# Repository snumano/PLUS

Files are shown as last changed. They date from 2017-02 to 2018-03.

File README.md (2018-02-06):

# Otto DIY+
"Otto DIY with steroids" 

This Repository have all open source files for Otto DIY+ an interactive robot that anyone can make!,
Otto DIY + can make everything that Otto DIY does + Bluetooth + APP + switch + sensors + strength +... anything you might expand feel FREE to add and contribute. for LED Matrix we have a separate repository here https://github.com/OttoDIY/Matrix_hands
Is completely open source, Arduino compatible, 3D printable, once you have all components and tools you will be able to build your own Otto
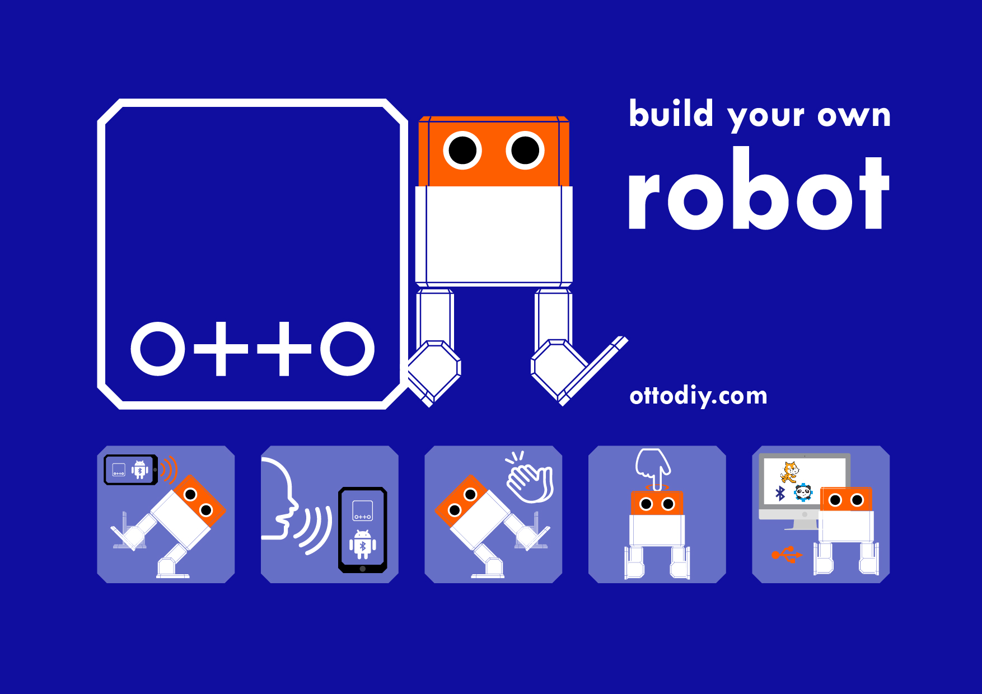
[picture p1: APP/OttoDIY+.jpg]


This is a more advanced version requires some expertise and patience, if you want to start slow as a beginner  please go to [Otto DIY repository](https://github.com/OttoDIY/DIY)

Start by [downloading all files here](https://github.com/OttoDIY/PLUS/archive/master.zip)

## For the hardware
Gather all the off the shelf parts in the BOM file that you'll need for this assembly, then 3d print the  .stl files and then follow the instruction manual to build your own robot.

## For the quick start programming and learners
1. download mBlock.cc V3; is an opensource software released by MakeBlock for easy programming Robot by Drop and Drag blocks. Based on Scratch 2.0 (MIT), beside sharing the great Feature of Scratch, mBlock also integrated an Arduino Code generator for upload program into Arduino based Hardware.
2. install Otto Extension in mBlock software use Arduino mode
3. drag and drop functions, dance, sounds and conditionals from robot Otto blocks
4. connect and check COM port
5. upload your own code! 

## For the advanced programming
1. Download & Install Arduino IDE: https://www.arduino.cc/en/Main/Software also this driver if you have a clone board: http://www.wch.cn/download/CH341SER_EXE.html for PC, or http://www.wch.cn/download/CH341SER_MAC_ZIP.html for MAC
2. Copy all libraries to C:\Users\user\Documents\Arduino\libraries (or wherever your library folder is installed):
3. Open  any .ino code, make sure in tools you have "Board: Arduino Nano" "Processor ATmega328" and your Otto is connected to the corresponding port
4. Upload code to your Otto
5. Check or setup your Bluetooth module baud rate
6. Upload the Bluetooth APP code to Otto DIY+
7. Play with the APP
8. Share in our Otto builder Facebook group https://www.facebook.com/ottodiy/groups/

### Otto DIY+ is  design using Autodesk Fusion 360
So is completely parametric and precise to adjust tolerances
[You can modify it for customization](https://gallery.autodesk.com/fusion360/projects/otto-diyplus) or further improvements

### Hall of fame Otto builders list
Our broad community is awesome! we have been developing and improving OttoDIY project together ;)

| contribution  | date | builder name | country |
| --- | --- | --- | --- |
| oscillator algorithm library| Jan 2015 | Obijuan | Spain  |
| inventor of Zowi 3D printable | Dec 2015  | Javier Isabel |Spain |
| Bobwi (combination of Bob and Zowi  | Jan 2016  |G4alileo |Spain  |
| BT, battery, nose LED RGB, touch and tilt | April 2016 |Davor Levstek  |Croatia |
| Robonino with voice control |May 2016|Santiago|Spain |
| Calibration tool  | June 2016 |Rafael López  |Spain |
| FreeCAD model|August 2016|Juan Carlos López Sánchez |Spain |
| ESPOtto voice | Sept 2016 |Gustavo Reynaga |Mexico|
| Otto arms |Sept 2016|Jason Leung| Hong Kong |
| Google Play android APP  | Oct 2016 |Juan Felix Mateos |Spain |
| Switch alternative |Dec 2016|Robert Holt |United States |
| Custom PCB, OttoDIY+ repository | Jan 2017 |Jason Snow |England |
| Single ladies dance| Jan 2017  |brico3D |Spain |
| Nose and DIY APP |Feb 2017|Andrés Fernández Muñoz|Spain |
| feedback  | March 2017 |Frank Lopez |United States |
| feedback | March 2017  |Octavio P Nogueira |Brazil  |
| feedback  | March 2017  |tritri62|??? |
| Custom PCB | 	March 2017 |Marco|Italy |
| Laser cut Otto |March 2017|Florian Festi|Germany |
| XXL Head |March 2017|Markus Otte |Germany |
| XGoBroRobo IR control |March 2017|Jonathan Hess |Germany |
| Easy BT Easy HC-06 | May 2017  |Pablo E. García Palacios  |Spain |
| Custom PCB, battery booster, noise detection | April 2017|Pedro 51|France |
| graphical coding  | June 2017  |Liao Ping Lun  |China |
| Otto bender mod| June 2017  |bricogeek |Spain |
| remote control | July 2017  |Jayesh Chauhan |India  |
| Customizable Otto 3D print |July 2017|Brandon Bowles |United States |
| quadruped Otto | August 2017  |quadruped |China |
| control from laptop | August 2017  |SungHyun Ryu |South Korea |
| touch code | September 2017  |Alberto |Spain |
| Otto wheels | September 2017 |Jason Snow |England |
| Tito +| September 2017 |Jason Snow |England |
| 6 modes code | October 2017  |Davor Levstek  |Croatia |
| Otto accessories| October 2017  |Lucid Wolf|Australia |
| Otto accessories Halloween  | October 2017  |Trish Davies  |Australia |
| mbloc scratch graphical coding| November 2017  |Hien Phan |Vietnam |
| Otto Santa Claus| December 2017  |Dreamfactory  |Argentina |
| Otto Nutcraker| December 2017  |Dreamfactory  |Argentina |
| SelfProgramming| December 2017  |YoJuLab  |South Korea |
| open APP inventor | January 2018 |Jason Snow |England |
| LED eyes | January 2018 |Mr. Chan|China |
| Otto learning| January 2018  |Hien Phan |Vietnam |
| new APP BETA | February 2018 |Jason Snow |England |

Special thanks to all these #Ottobuilder that made and are making this project evolve and accessible to everyoone in the world. If we skip one please tell us!

### Pending  to develop idea list
Feel free to grab and mix ideas from this table for your Otto and if you are nice person please share with all the community

| Function-Feature  | sensor(input) | movement (output) | 
| --- | --- | --- |
| drumer  |microphone|hands+stick|
| Car-balancing  |accelerometer|4x4 wheels|
| Sumo |IR|wheels+bumper|
| omniwheel |magnet switch|wheels+rollers|
| Train |IR|Steam generator|
| Humanoid |variable resistor modes|+servos control|
| Spider 6-8 legs |gestures|+vibrators|
| hover or drone |accelerometer|+DC motor control|
| look around xiaofang |timer|new head|
| writer |encoders|DC+ pen holder|
| following line |IR+encoders|step motors|
| Bubbles |light|DC fan|
| crane |Buttons|+servos control|
| Gripper |Tilt Sensor|+servo|
| reaction to music  |keepon|vibrators|
| Follow music | MP3 SD card|disco lights|
| Voice commands |telegram|multiple boards|
| clap rhythm |microphone|vibrators|

## License CC-BY-SA
<br /><span xmlns:dct="http://purl.org/dc/terms/" property="dct:title">Otto DIY</span> by <a xmlns:cc="http://creativecommons.org/ns#"  property="cc:attributionName"> [www.ottodiy.com](http://www.ottodiy.com) </a> is licensed under a <a rel="license" href="http://creativecommons.org/licenses/by-sa/4.0/">Creative Commons Attribution-ShareAlike 4.0 International License</a>.

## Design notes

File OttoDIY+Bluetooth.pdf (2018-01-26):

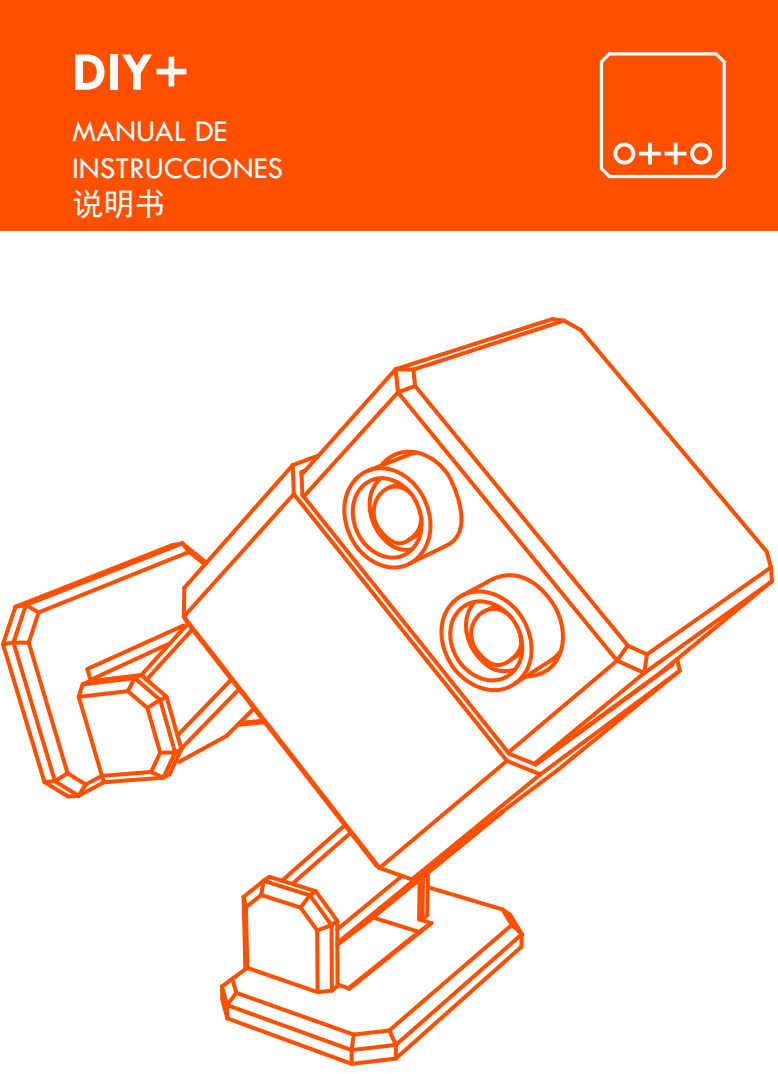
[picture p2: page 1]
DIY+; MANUAL DE INSTRUCCIONES 说明书

Estos pasos son para configurar los módulos de Bluetooth HC-05 y HC-06 Las conexiones son las siguientes:
HC-05 GND --- Arduino GND Pin
HC-05 VCC (5V) --- Arduino 5V
HC-05 TX --- Arduino Pin 10 (soft RX)
HC-05 RX --- Arduino Pin11 (soft TX)
HC-05 Key (PIN 34) --- Arduino Pin 9

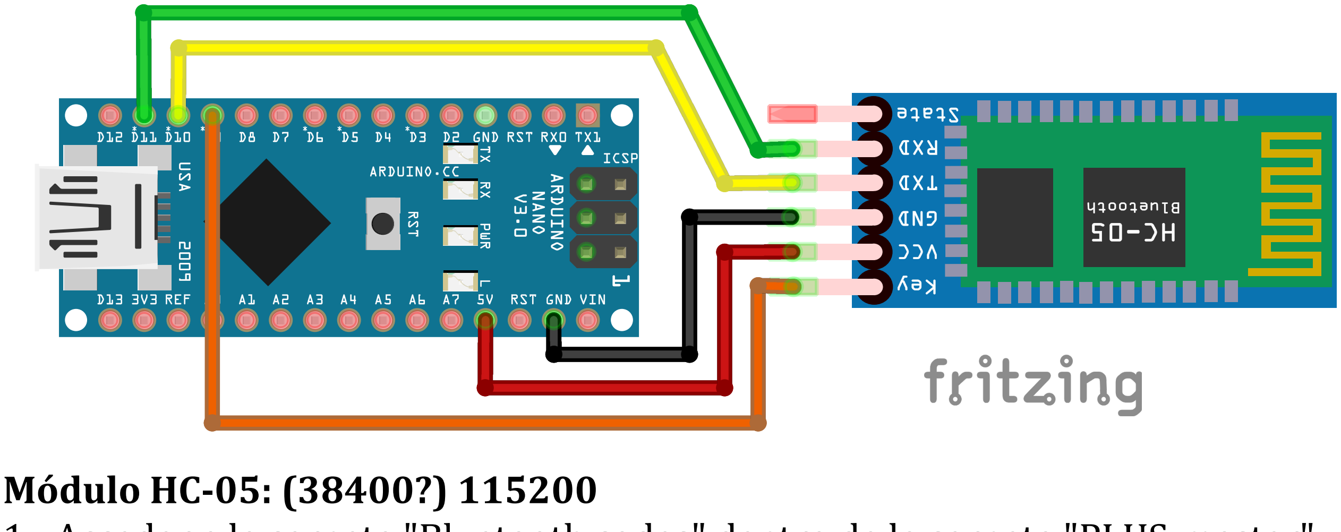
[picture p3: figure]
Módulo HC-05: (38400?) 115200

1.- Acceder a la carpeta "Bluetooth codes" dentro de la carpeta "PLUS-master" y cargar el código HC05_BT_Config.ino (https://github.com/OttoDIY/PLUS/blob/master/Bluetooth%20codes/HC05_BT_config/HC05_BT_config.ino) al Arduino Nano.
2.- Desconectar el Arduino Nano del USB y realizar la conexión del módulo de Bluetooth como se indica en la imagen de arriba, sin conectar aún el voltaje de alimentación VCC.
3.- Conectar de nuevo el Arduino Nano al USB y entonces conectar el cable del Bluetooth a VCC tal que entre en el modo de comando AT. El led del Bluetooth debería comenzar a destellar lentamente, al rededor de una vez cada 2 segundos. (si esto no llegara a suceder, intente mantener pulsado el botón de reset del módulo Bluetooth mientras lo alimenta a VCC)
4.- Abra el monitor serie de la IDE de Arduino, seleccione la tasa de transmisión a 9600 baudios, y en final de línea ambos NL & CR.
5.-Introduzca AT y presione Enter; (si todo es correcto, el Bluetooth debería responder con un OK y entonces proceder a introducir los siguientes comandos): AT+NAME=Zowi (Establecemos el nombre)
AT+PSWD=1234 (Establecemos el código de paridad) AT+UART=115200,1,0 (Establecemos la tasa de transmisión)
AT+POLAR=1,0 " ( Habilitamos el pin STATE para ser utilizado como reset para programar Arduino a través del módulo Bluetooth)
Por último, cerrar el monitor serie y realizar las conexiones electrónicas de Otto.

Módulo HC-06: (9600?) 115200
Para el módulo HC-06 las cosas son un poco más simples debido a que siempre se encuentra en modo de comando AT cuando no se encuentra conectado a nada. La desventaja es que el módulo HC-06 no puede ser usado para cargar códigos al Arduino debido a que no posee reset.
Para configurar el módulo:
1.- Cargar el código HC06_BT_config.ino (https://github.com/OttoDIY/PLUS/blob/master/Bluetooth%20codes/HC06_BT_config/HC06_BT_config.ino) al arduino Nano
2.- Desconectar el Arduino Nano del USB
3.- Conectar el módulo Bluetooth al Arduino Nano como se indica en la imagen de
abajo:
HC-06 GND --- Arduino GND Pin
HC-06 VCC (5V) --- Arduino 5V
HC-06 TX --- Arduino Pin RX
HC-06 RX --- Arduino Pin TX

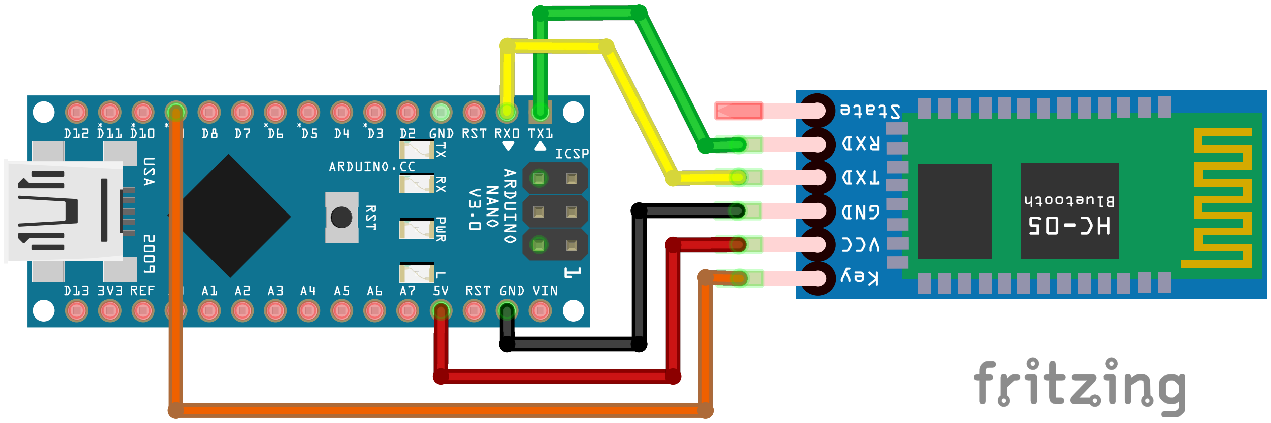
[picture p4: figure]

2.- Desconectar el Arduino Nano de la usb y realizar la conexión del módulo de Bluetooth como se indica en la imagen de arriba, sin conectar aún el voltaje de alimentación VCC.
3.- Encender el Arduino Nano y después de al rededor de 10 segundos todo debería estar terminado y tu módulo Bluetooth debería estar configurado (LED 13 debería comenzar a destellar).
Por último, realizar las conexiones electrónicas de Otto.

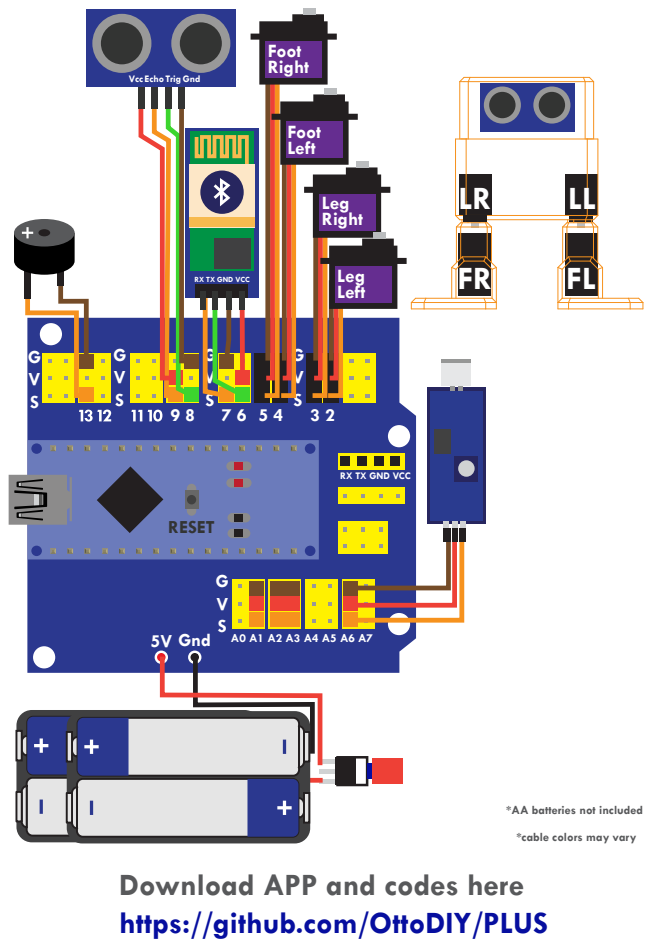
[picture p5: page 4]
RESET; 5V Gnd; Foot Right; FL RX TX GND VCC; Leg; Left; Leg Right; Foot Left; Vcc; TrigEcho; Gnd

RX TX GND VCC

*AA batteries not included
*cable colors may vary

Download APP and codes here
https://github.com/OttoDIY/PLUS

Código Principal
Después de configurar el módulo Bluetooth, desconecte de nuevo el módulo Bluetooth y cargue el siguiente código al Arduino Nano:
OTTO_BT.ino (https://github.com/OttoDIY/PLUS/blob/master/Bluetooth%20codes/OTTO_BT/OTTO_BT.ino)
Después de cargar exitosamente el código, conecte el módulo Bluetooth de nuevo y estará listo para el emparejamiento.

APP para Android:
Tú puedes crear tu propia APP!
Descarga la última APK aquí (https://github.com/OttoDIY/PLUS/tree/master/APP)
Usando la aplicación AppInventor desarrollada por el MIT, usa nuestra plantilla para modificar y crear tu propia aplicación móvil.
O debido a que Otto también es compatible con Zowi, tú puedes usar la APP desarrollada por BQ
Descarga Aquí la (https://play.google.com/store/apps/details?id=com.bq.zowi&hl=es) App Oficial de Zowi desarrollada por BQ
Descargue el código Otto_BT_ZowiAPP.ino (https://github.com/OttoDIY/PLUS/blob/master/Bluetooth%20codes/Otto_BT_ZowiAPP/Otto_BT_ZowiAPP.ino)
Instala y abre la APP Zowi para Android, empareja los dispositivos e ignora los mensajes de advertencia que dicen que el código fué modificado o similar. Nota: Recuerda copiar todas las librerías en la carpeta de Arduino

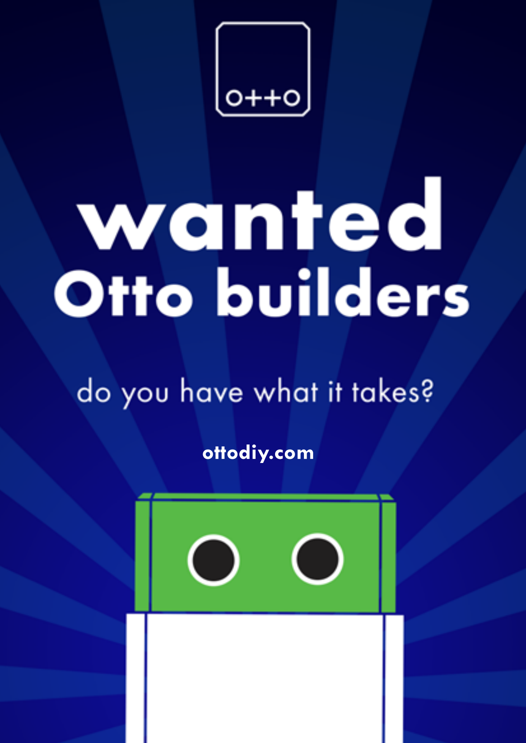
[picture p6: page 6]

ottodiy.com

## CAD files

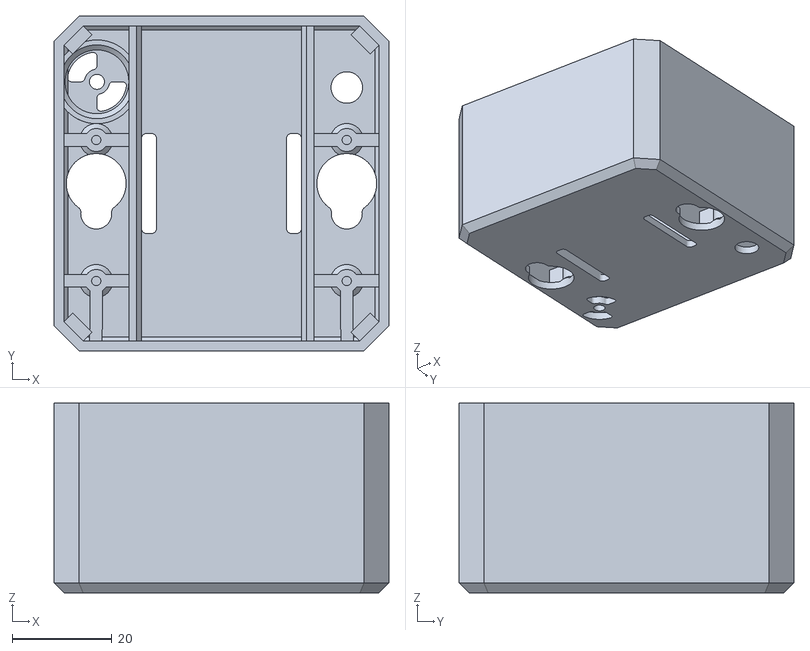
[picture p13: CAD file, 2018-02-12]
3D print/OttoDIY+_Body_v05.stl
67.0 x 67.0 x 38.0

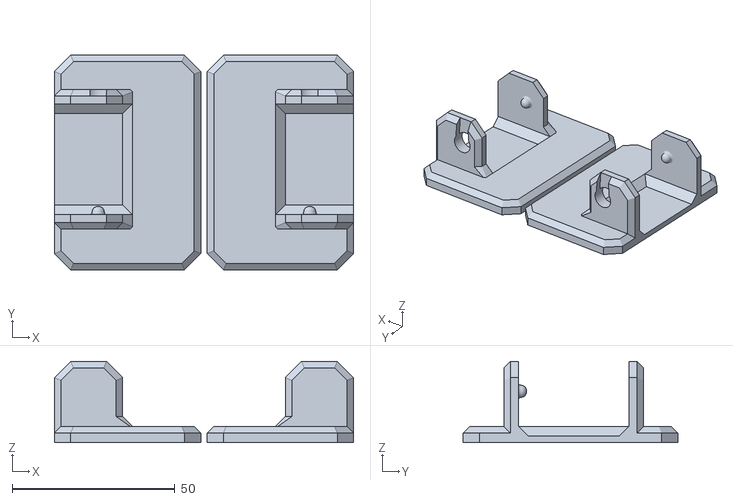
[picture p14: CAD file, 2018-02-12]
3D print/OttoDIY+_Feet_v06.stl
92.0 x 66.0 x 25.0

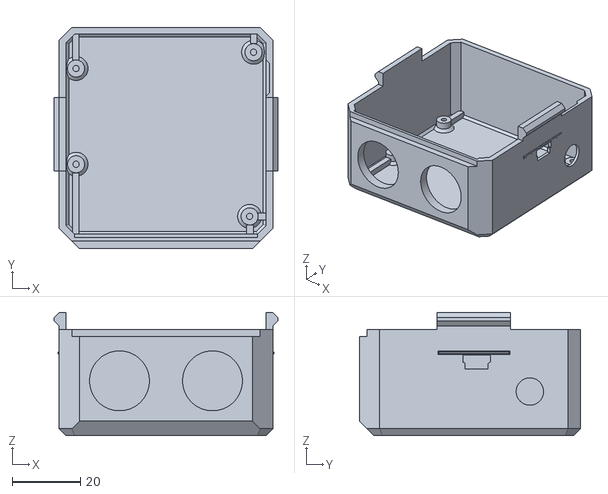
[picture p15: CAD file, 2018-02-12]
3D print/OttoDIY+_Head_v05.stl
65.5 x 64.7 x 36.0

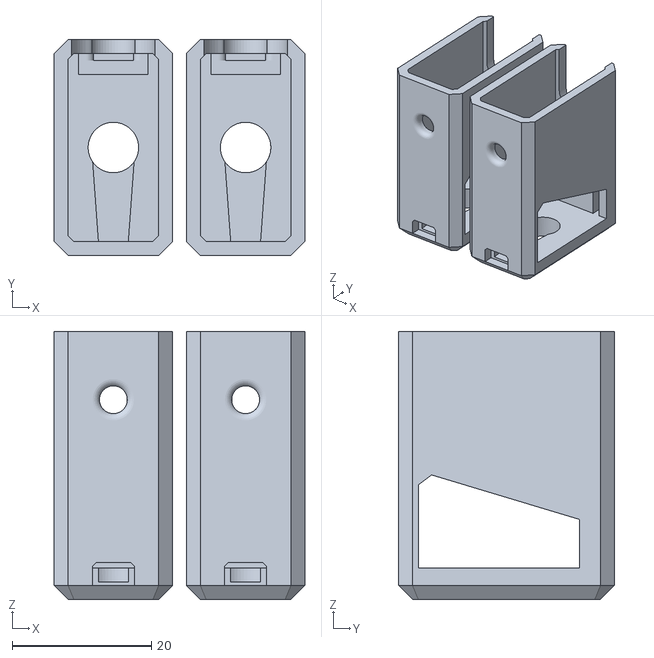
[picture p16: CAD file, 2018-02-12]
3D print/OttoDIY+_Legs_v06.stl
36.0 x 31.0 x 38.5

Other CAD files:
3D print/OttoDIY+_CUSTOM.scad

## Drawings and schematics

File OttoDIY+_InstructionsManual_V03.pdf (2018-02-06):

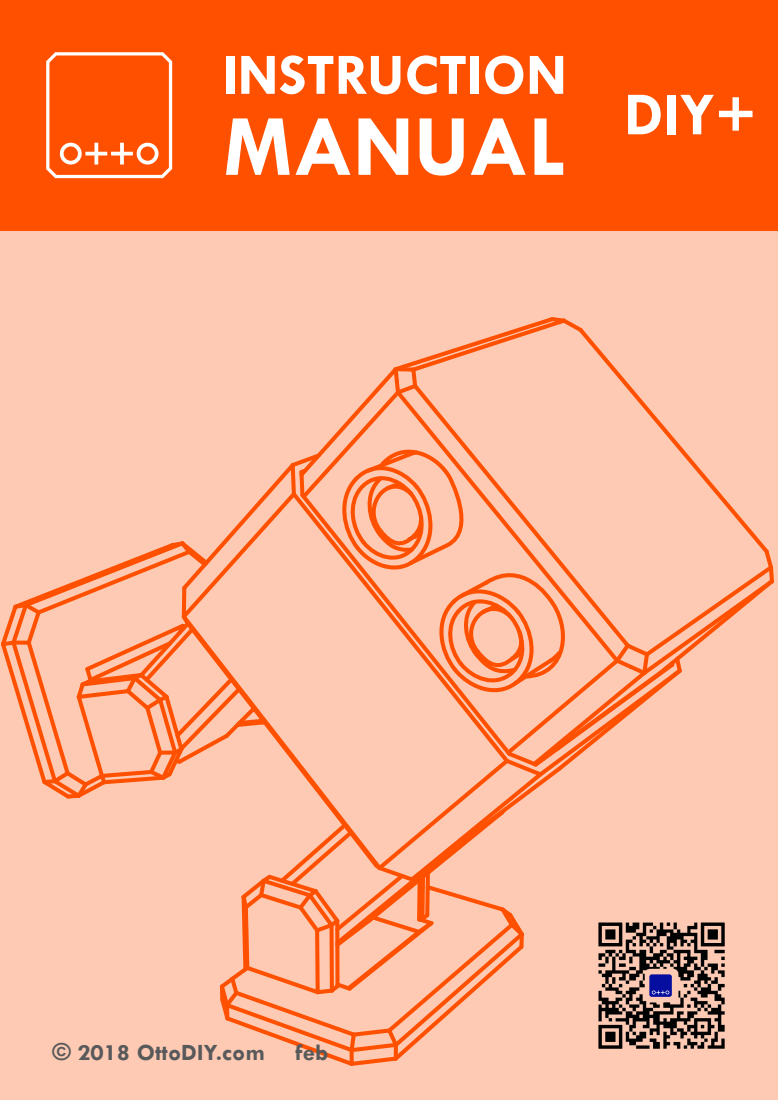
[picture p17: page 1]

© 2018 OttoDIY.com feb

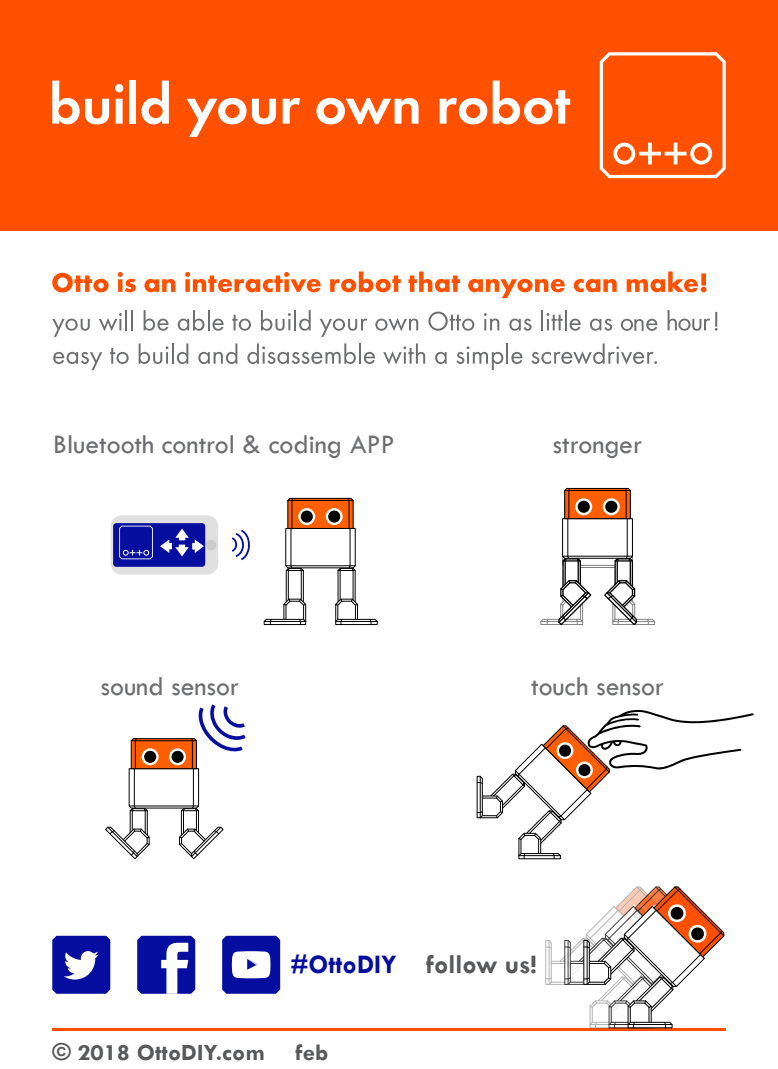
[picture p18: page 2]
sound sensor; touch sensor; stronger

Bluetooth control & coding APP

#OttoDIY follow us!

© 2018 OttoDIY.com feb

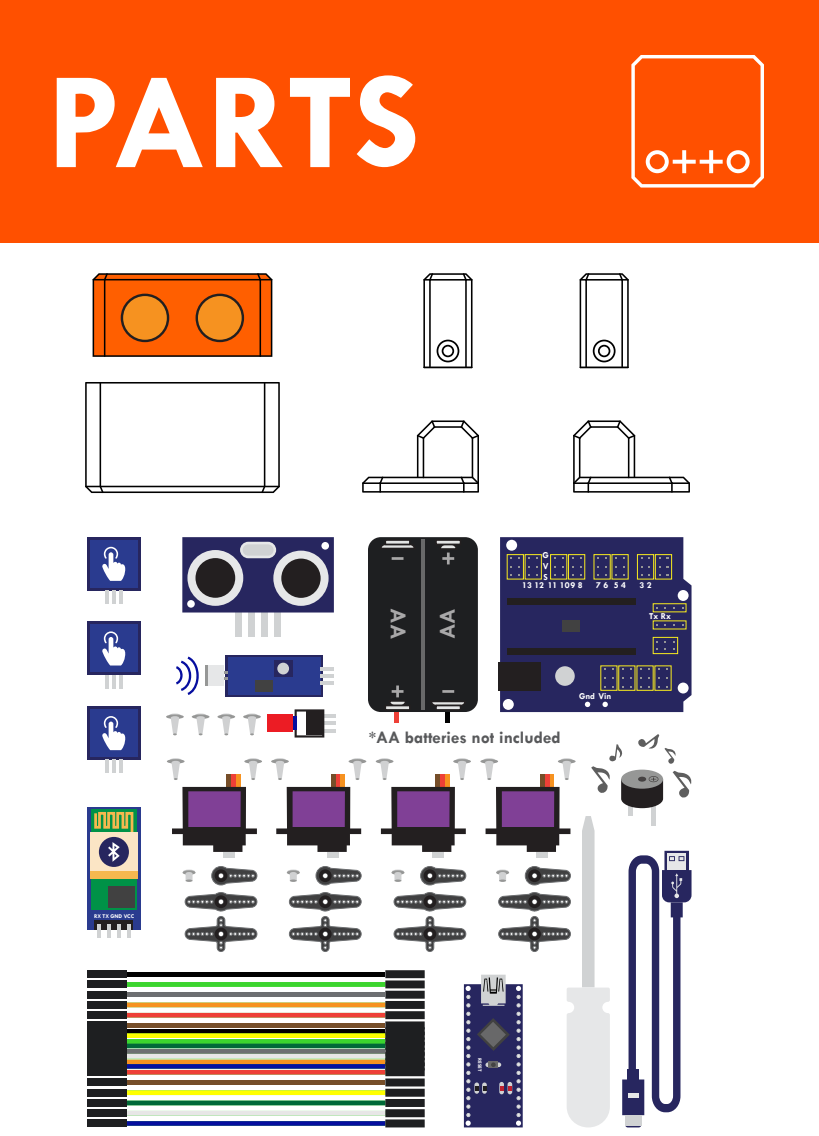
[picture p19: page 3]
Gnd Vin

*AA batteries not included RESET

RX TX GND VCC

a

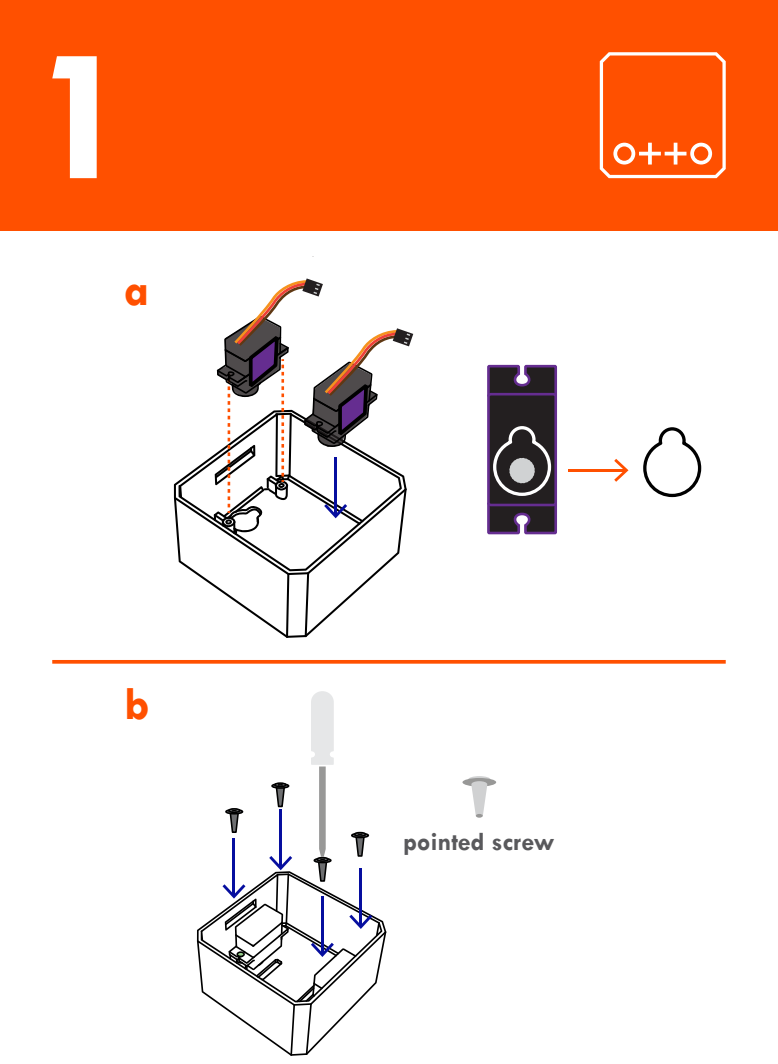
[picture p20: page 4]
pointed screw

a

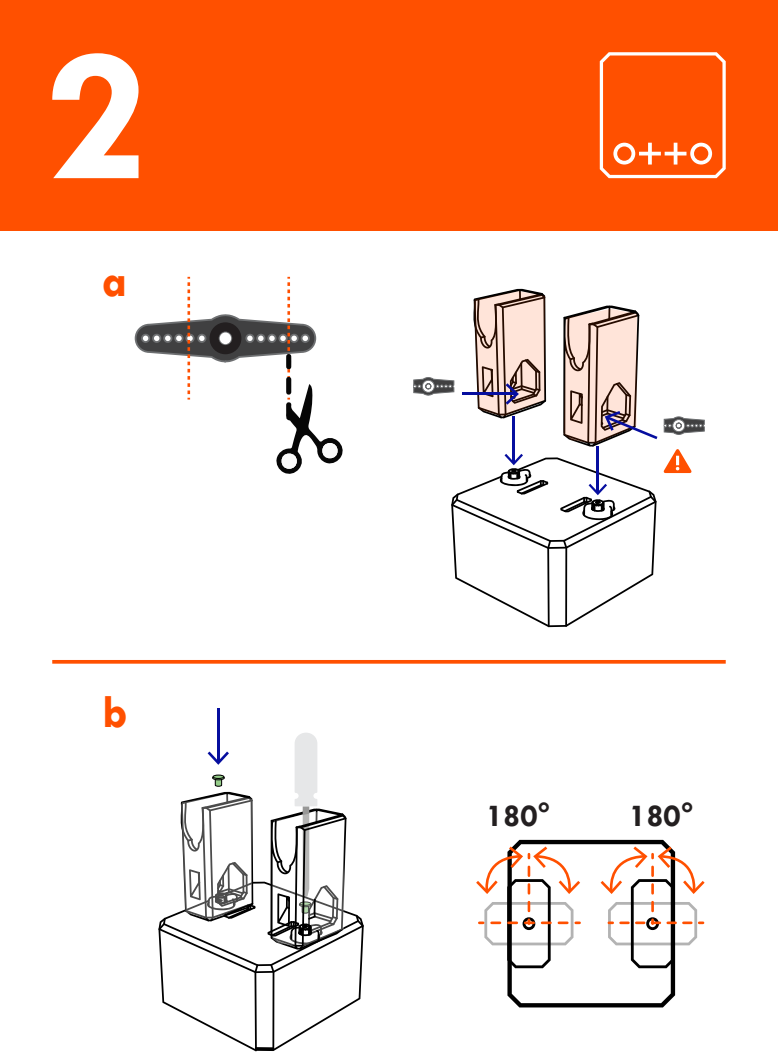
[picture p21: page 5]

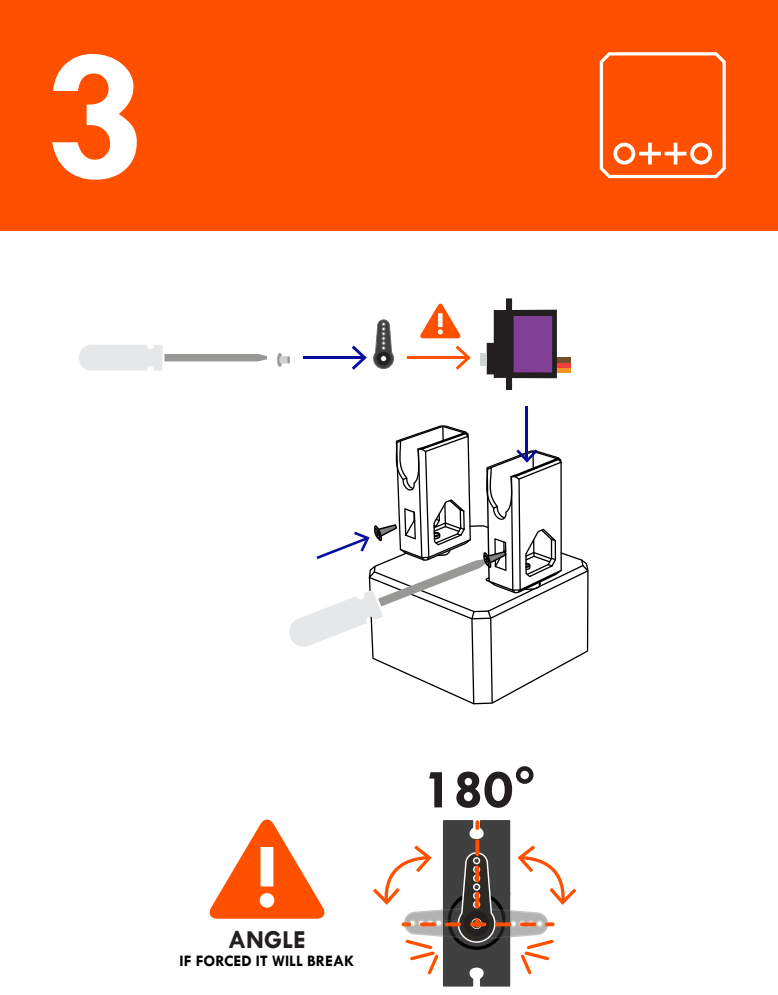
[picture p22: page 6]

ANGLE IF FORCED IT WILL BREAK

ab

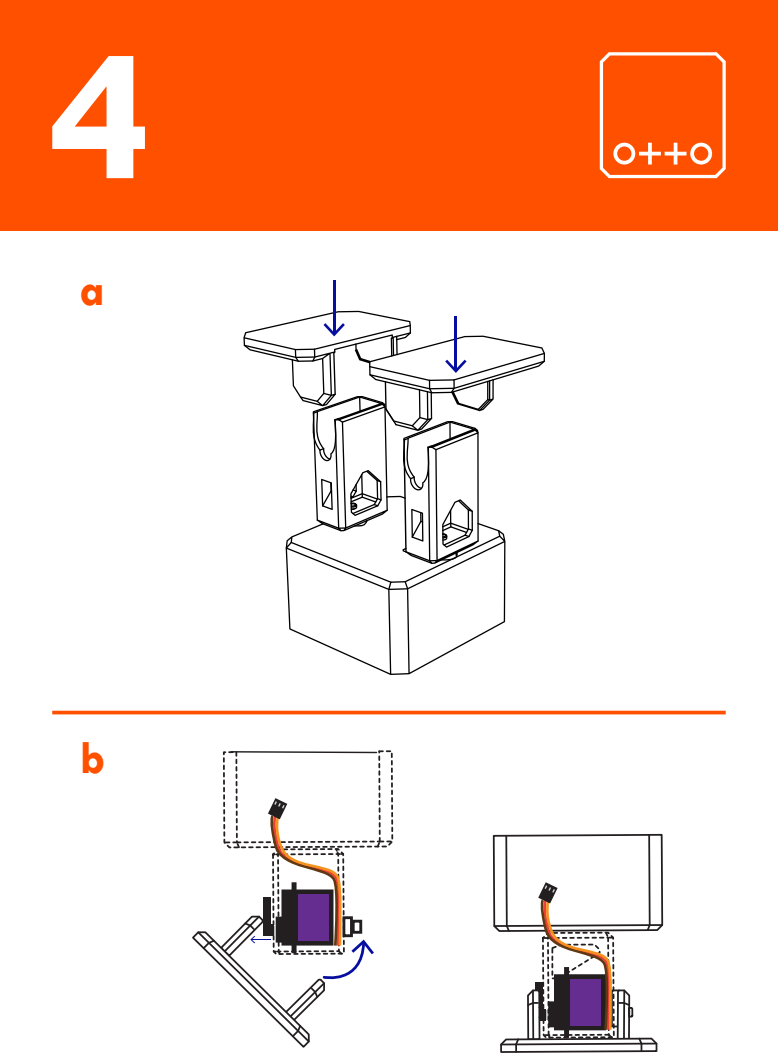
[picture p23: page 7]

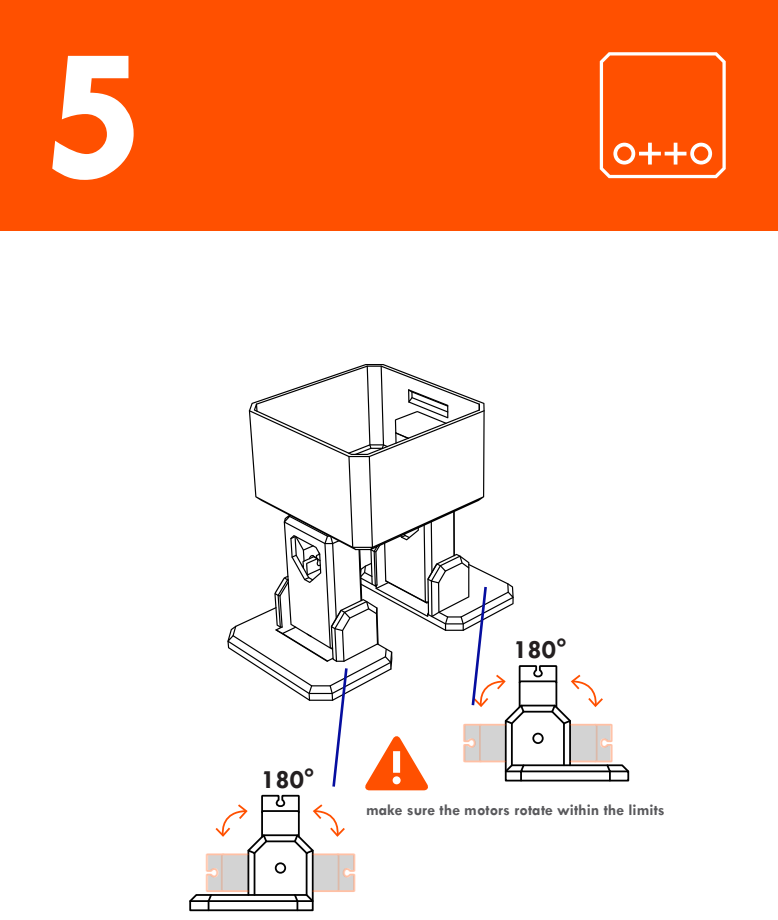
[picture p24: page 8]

make sure the motors rotate within the limits

a

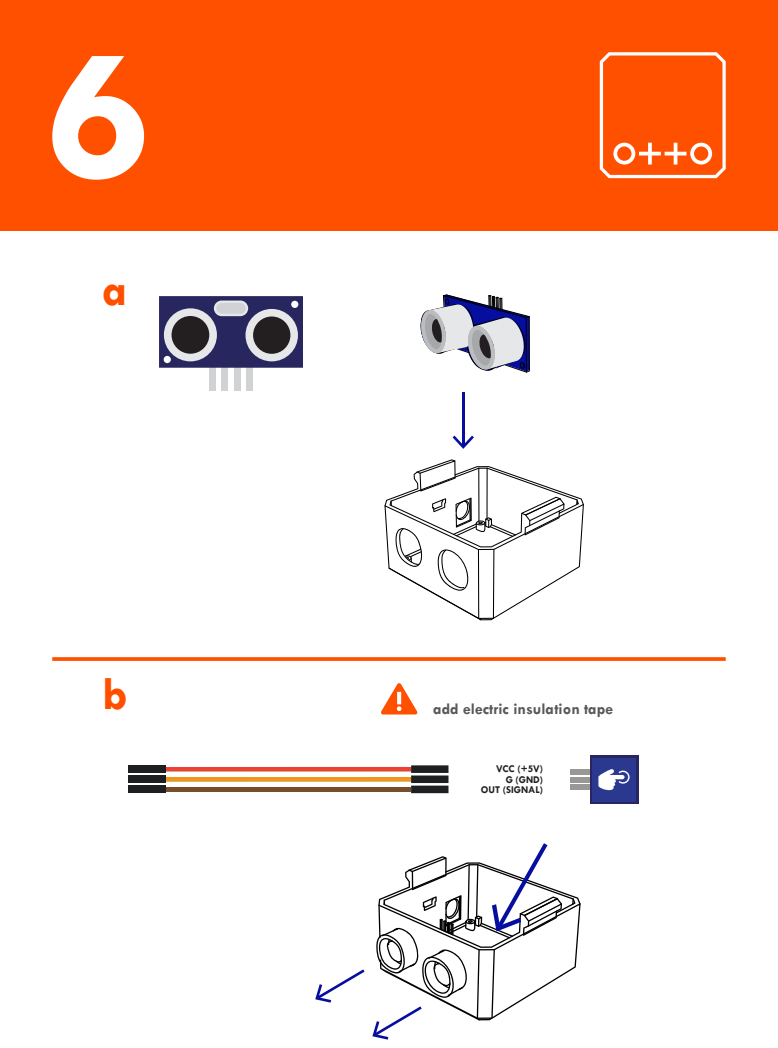
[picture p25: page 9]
add electric insulation tape; VCC (+5V) G (GND) OUT (SIGNAL)

a

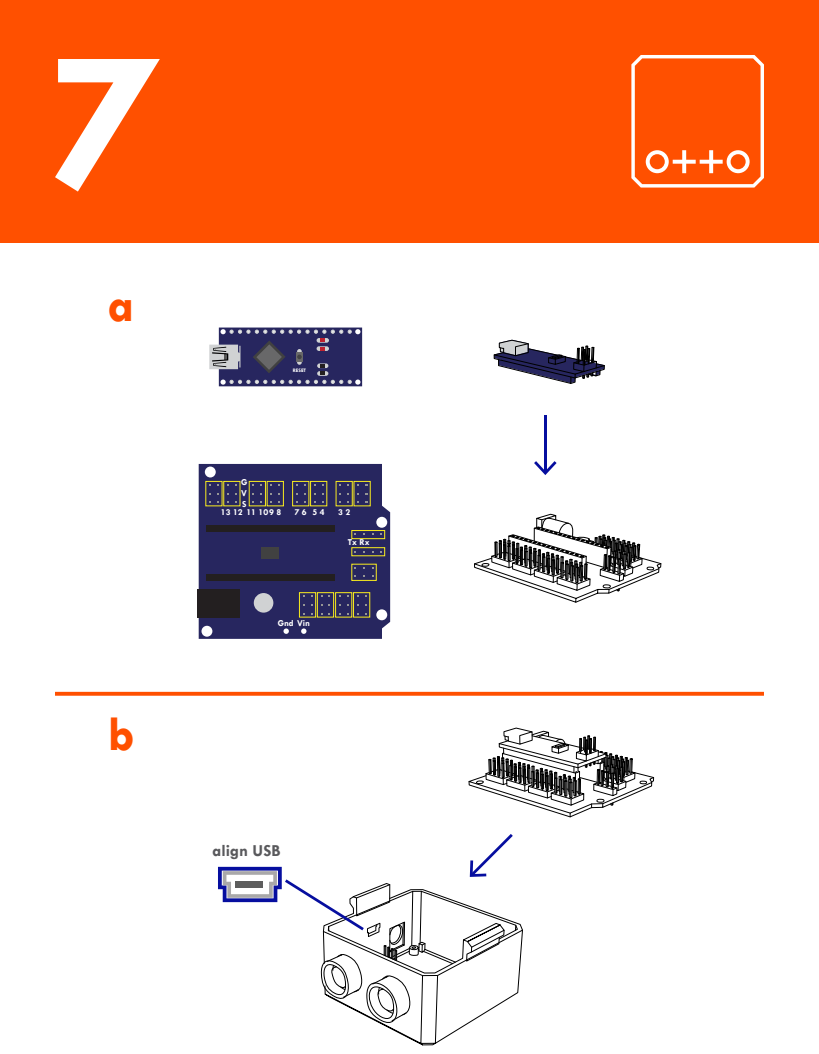
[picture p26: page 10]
RESET; Gnd Vin; align USB

a

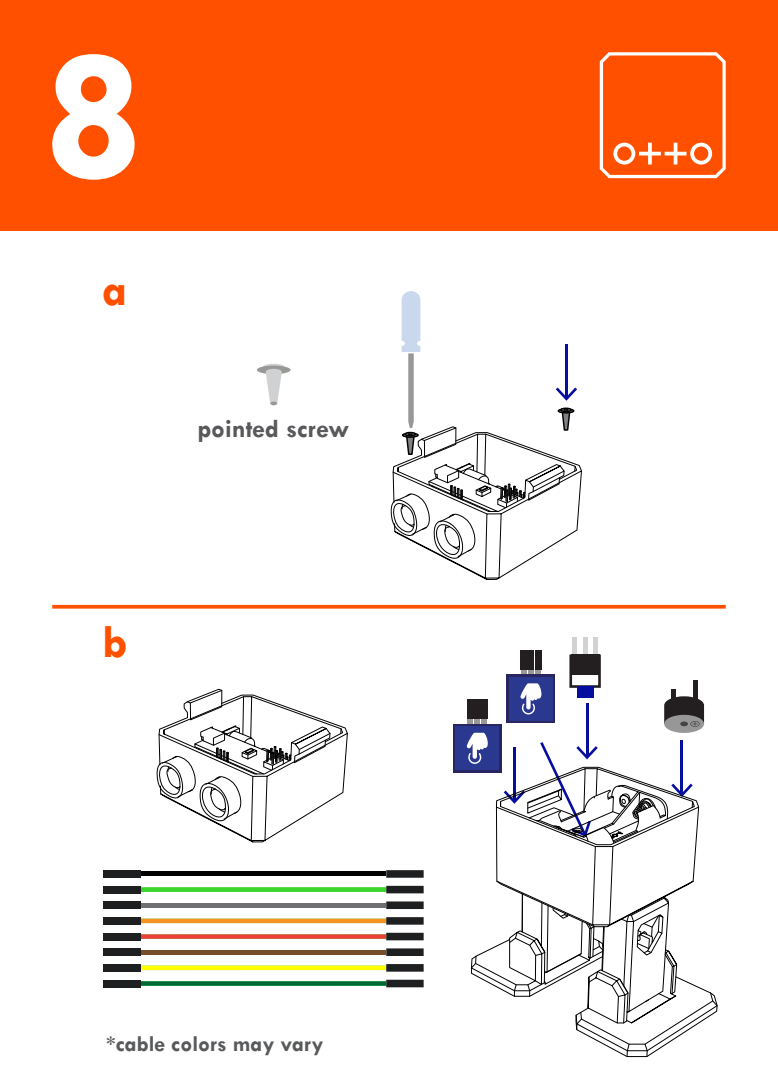
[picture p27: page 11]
pointed screw

*cable colors may vary

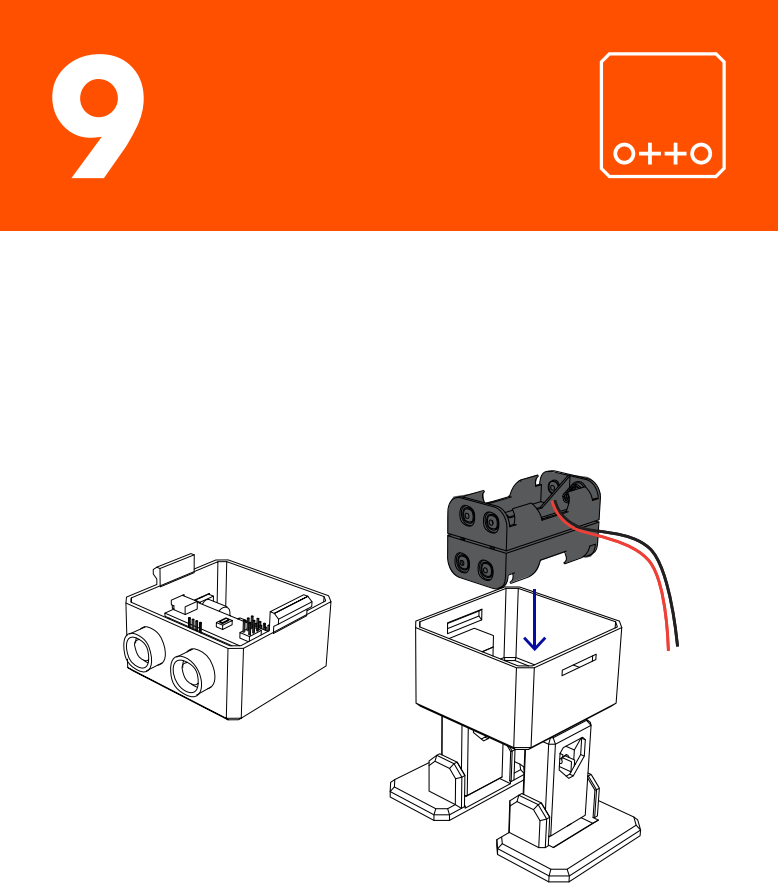
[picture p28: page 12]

RESET; 5V Gnd; Foot Right; sound sensor; FL RX TX GND VCC; Leg; Left; Leg Right; Foot Left; G (GND) V (+5V) S (SIGNAL); Vcc EchoTrigGnd

RX TX GND VCC

*cable colors may vary
*AA batteries not included
before using batteries test with USB first

## connect and power with USB and test movements


before close and using AA batteries

Bluetooth module; © 2018 OttoDIY.com feb; *AA batteries not included

external auxiliary POWER port 6-12V
ultrasound sensor for objet detection

USB for programming and POWER
NOT FOR BATTERY RE-CHARGE

quick snap assembly (inside)

2 legs for walk and dance

4AA batteries* last up to 2 hours.

robot beeps that represent moods

remix; expand...; modify

Download android APP and codes here
https://github.com/OttoDIY/PLUS

#OttoDIY share
post your creations!
customize

© 2018 OttoDIY.com feb


# ottodiy.com

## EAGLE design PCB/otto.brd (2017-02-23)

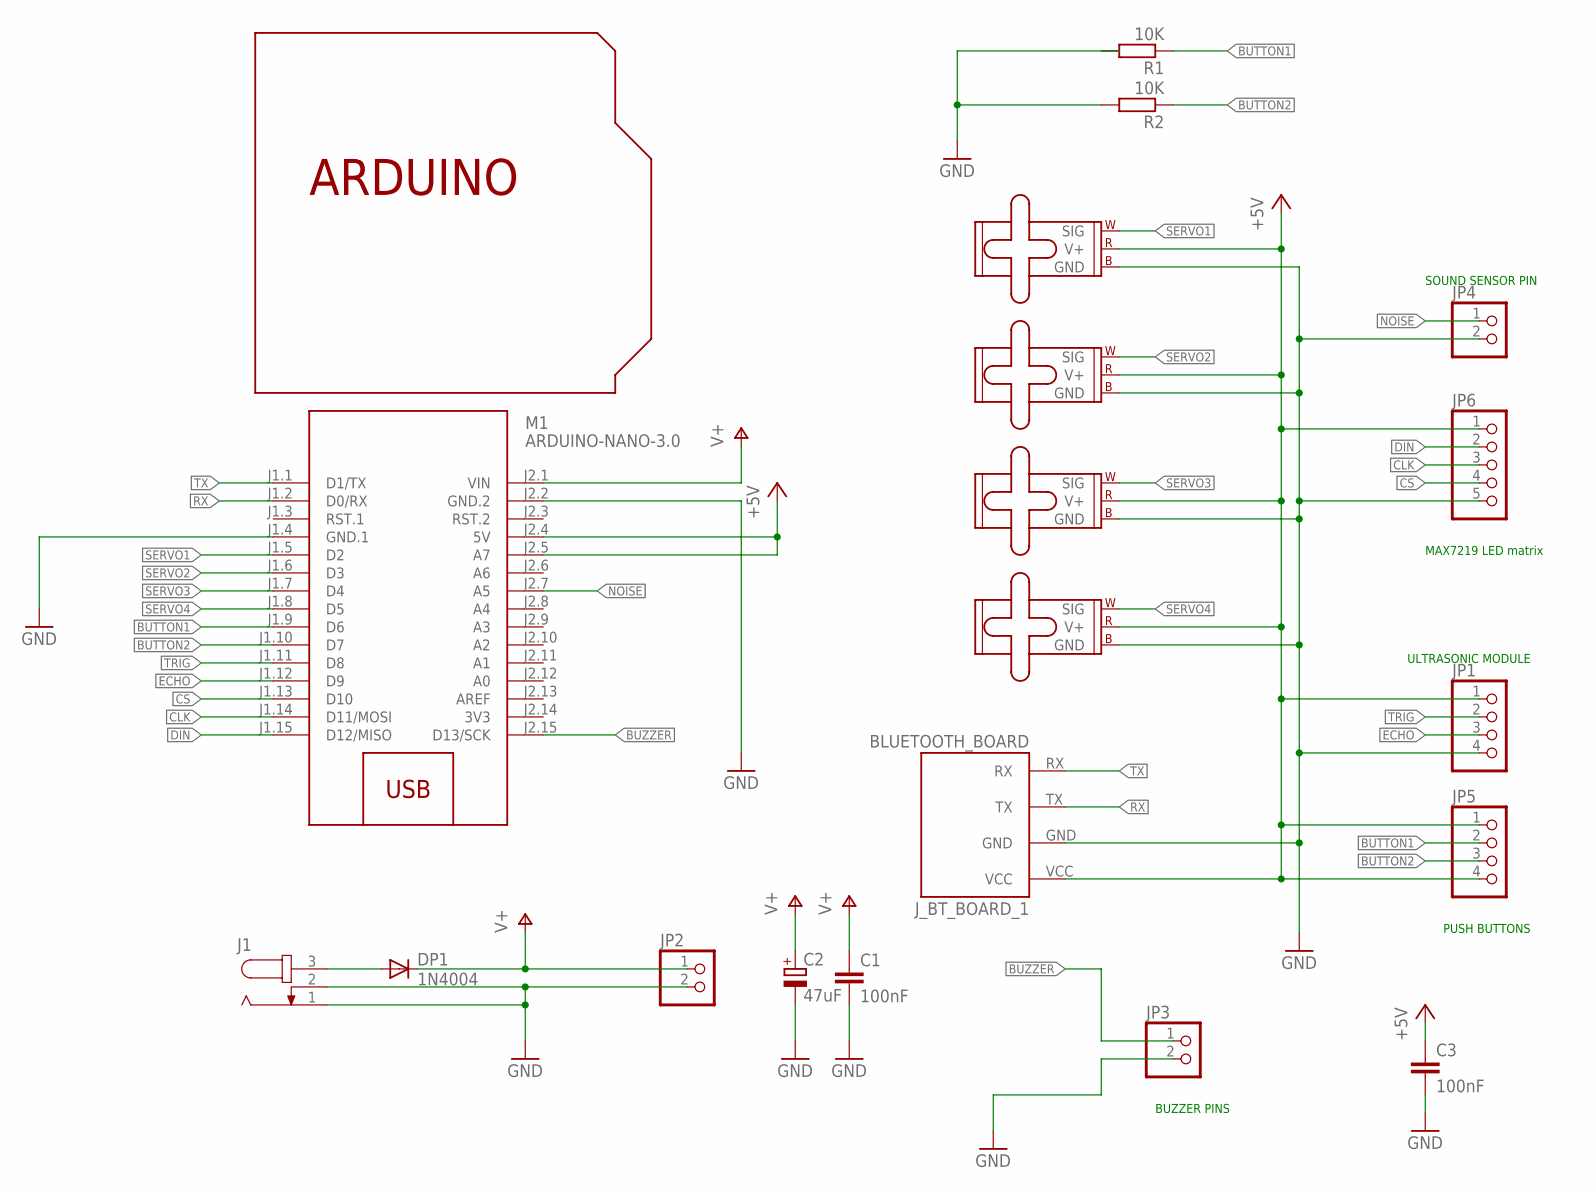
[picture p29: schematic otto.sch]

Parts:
C1, C3: 100nF; C025-025X050
C2: 47uF; 140CLH-0810
DP1: 1N4004; DO41-10
J1: JACK-PLUG0; SPC4077
JP1, JP5: PINHD-1X4; 1X04
JP2, JP3, JP4: PINHD-1X2; 1X02
JP6: PINHD-1X5; 1X05
J_BT_BOARD_1: BLUETOOTH_BOARD; BT_BOARD_FOOTPRINT
M1: ARDUINO-NANO-3.0
M2, M3, M4, M5: SMALL_SERVO; 1X03
R1, R2: 10K; 0207/7
U$1: SHIELDSMALL; ARDUINOSHIELDSMALL

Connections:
3V3: M1.J2.14 (3V3)
+5V: C3.1, JP1.1, JP5.1, JP5.4, JP6.1, J_BT_BOARD_1.VCC, M1.J2.4 (5V), M1.J2.5 (A7), M2.2 (V+), M3.2 (V+), M4.2 (V+), M5.2 (V+)
BUTTON1: JP5.2, M1.J1.9 (D6), R1.1
BUTTON2: JP5.3, M1.J1.10 (D7), R2.1
BUZZER: JP3.1, M1.J2.15 (D13/SCK)
CLK: JP6.3, M1.J1.14 (D11/MOSI)
CS: JP6.4, M1.J1.13 (D10)
DIN: JP6.2, M1.J1.15 (D12/MISO)
ECHO: JP1.3, M1.J1.12 (D9)
GND: C1.2, C2.-, C3.2, J1.1, J1.2, JP1.4, JP2.2, JP3.2, JP4.2, JP6.5, J_BT_BOARD_1.GND, M1.J1.4 (GND.1), M1.J2.2 (GND.2), M2.3 (GND), M3.3 (GND), M4.3 (GND), M5.3 (GND), R2.2
unnamed: DP1.A, J1.3
NOISE: JP4.1, M1.J2.7 (A5)
RX: J_BT_BOARD_1.TX, M1.J1.2 (D0/RX)
SERVO1: M1.J1.5 (D2), M2.1 (SIG)
SERVO2: M1.J1.6 (D3), M3.1 (SIG)
SERVO3: M1.J1.7 (D4), M4.1 (SIG)
SERVO4: M1.J1.8 (D5), M5.1 (SIG)
TRIG: JP1.2, M1.J1.11 (D8)
TX: J_BT_BOARD_1.RX, M1.J1.1 (D1/TX)
V+: C1.1, C2.+, DP1.C, JP2.1, M1.J2.1 (VIN)

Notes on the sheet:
MAX7219 LED matrix
ULTRASONIC MODULE
PUSH BUTTONS
SOUND SENSOR PIN
BUZZER PINS

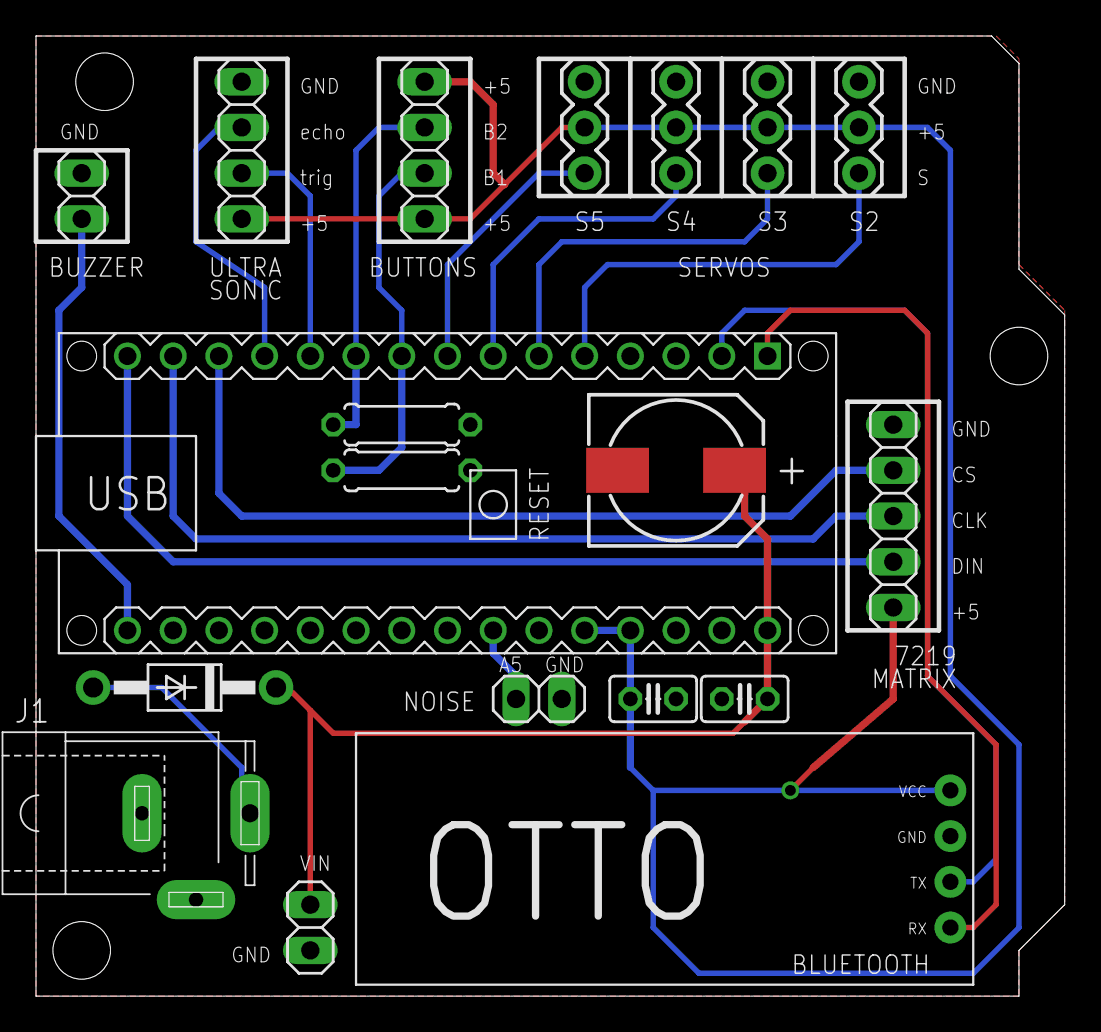
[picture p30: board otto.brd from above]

Board: 2 copper layers, 57.2 x 53.3 mm, 20 parts (0 on the bottom side), 19 nets.

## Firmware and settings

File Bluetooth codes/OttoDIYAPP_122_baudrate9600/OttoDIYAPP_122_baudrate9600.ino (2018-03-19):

//----------------------------------------------------------------
//-- Otto DIY Android APP 122 code
//-- (c) (http://ottodiy.com) Released under a GPL licencse
//-- 03 March 2018
//-- Author: Jason Snow
//-----------------------------------------------------------------
//-- FEBRUARY 2017: modified for OttoDIY with MAX7219 MATRIX LED module
//-- allows OttoDIY to work with Zowi APP
//-- Jason Snow
//-- JANUARY 2018: modified for new OttoDIY App
//-- Jason Snow
//-----------------------------------------------------------------

#include <BatReader.h>
#include <US.h>
#include "MaxMatrix.h"
MaxMatrix ledmatrix=MaxMatrix(12,10,11, 1); //PIN  12=DIN, PIN 10=CS, PIN 11=CLK

//-- Library to manage serial commands
#include <OttoSerialCommand.h>
OttoSerialCommand SCmd;  //The SerialCommand object

//-- Otto Library
#include <Otto.h>
Otto Otto;  //This is Otto!
 
//---------------------------------------------------------
//-- First step: Configure the pins where the servos are attached
/*
         --------------- 
        |     O   O     |
        |---------------|
YR 3==> |               | <== YL 2
         --------------- 
            ||     ||
            ||     ||
RR 5==>   -----   ------  <== RL 4
         |-----   ------|
*/

  #define PIN_YL 2 //servo[0]
  #define PIN_YR 3 //servo[1]
  #define PIN_RL 4 //servo[2]
  #define PIN_RR 5 //servo[3]

// buzzer connected to pin 13

///////////////////////////////////////////////////////////////////
//-- Global Variables -------------------------------------------//
///////////////////////////////////////////////////////////////////

const char programID[]="Otto_APP_1"; //Each program will have a ID

const char name_fac='$'; //Factory name
const char name_fir='#'; //First name

//-- Movement parameters
int T=1000;              //Initial duration of movement
int moveId=0;            //Number of movement
int modeId=0;            //Number of mode
int moveSize=15;         //Asociated with the height of some movements

//---------------------------------------------------------
//-- Otto has 5 modes:
//--    * MODE = 0: Otto is awaiting  
//--    * MODE = 1: Dancing mode!  
//--    * MODE = 2: Obstacle detector mode  
//--    * MODE = 3: Noise detector mode   
//--    * MODE = 4: OttoPAD or any Teleoperation mode (listening SerialPort). 
//---------------------------------------------------------
volatile int MODE=0; //State of Otto in the principal state machine. 

unsigned long previousMillis=0;

int randomDance=0;
int randomSteps=0;
int REDled = 0;
int GREENled = 0;
int BLUEled = 0;
bool obstacleDetected = false;

///////////////////////////////////////////////////////////////////
//-- Setup ------------------------------------------------------//
///////////////////////////////////////////////////////////////////
void setup(){
  //Serial communication initialization
  Serial.begin(9600);  
  //Set the servo pins
  Otto.init(PIN_YL,PIN_YR,PIN_RL,PIN_RR,true);
  // set up Matrix display
  ledmatrix.init();
  ledmatrix.setIntensity(1);
  //Set a random seed
  randomSeed(analogRead(A6));
  //Setup callbacks for SerialCommand commands 
  SCmd.addCommand("S", receiveStop);      //  sendAck & sendFinalAck
  SCmd.addCommand("L", receiveLED);       //  sendAck & sendFinalAck
  SCmd.addCommand("T", recieveBuzzer);    //  sendAck & sendFinalAck
  SCmd.addCommand("M", receiveMovement);  //  sendAck & sendFinalAck
  SCmd.addCommand("H", receiveGesture);   //  sendAck & sendFinalAck
  SCmd.addCommand("K", receiveSing);      //  sendAck & sendFinalAck
  SCmd.addCommand("C", receiveTrims);     //  sendAck & sendFinalAck
  SCmd.addCommand("G", receiveServo);     //  sendAck & sendFinalAck
  SCmd.addCommand("R", receiveName);      //  sendAck & sendFinalAck
  SCmd.addCommand("E", requestName);
  SCmd.addCommand("D", requestDistance);
  SCmd.addCommand("N", requestNoise);
  SCmd.addCommand("B", requestBattery);   // 
  SCmd.addCommand("I", requestProgramId);
  SCmd.addCommand("J", requestMode);
  SCmd.addCommand("P", requestRGB);
  SCmd.addDefaultHandler(receiveStop);
  //Otto wake up!
  Otto.sing(S_connection);
  Otto.home();
 // Animation Uuuuuh - A little moment of initial surprise
 //-----
  for(int i=0; i<2; i++){
      for (int i=0;i<8;i++){  
        Otto.putAnimationMouth(littleUuh,i);
        delay(150);
      }
  }
  //Smile for a happy Otto :)
    Otto.putMouth(smile);
    Otto.sing(S_happy);
    delay(200);

  //If Otto's name is '#' means that Otto hasn't been baptized
  //In this case, Otto does a longer greeting
  //5 = EEPROM address that contains first name character
  if (EEPROM.read(5)==name_fir){ 
 
        Otto.jump(1,700);
        delay(200); 
        Otto.shakeLeg(1,T,1);  
        Otto.putMouth(smallSurprise);
        Otto.swing(2,800,20);  
        Otto.home(); 
  }

  Otto.putMouth(happyOpen);
  previousMillis = millis();

}
///////////////////////////////////////////////////////////////////
//-- Principal Loop ---------------------------------------------//
///////////////////////////////////////////////////////////////////
void loop() {
  if (Serial.available()>0 && MODE!=4){
  // test
    SCmd.readSerial();
    //MODE=4;
    Otto.putMouth(happyOpen);
  }
  switch (MODE) {

      //-- MODE 0 - Otto is awaiting
      //---------------------------------------------------------
      case 0:
      
        //Every 80 seconds in this mode, Otto falls asleep 
        if (millis()-previousMillis>=80000){
            OttoSleeping_withInterrupts(); //ZZzzzzz...
            previousMillis=millis();         
        }

        break;
      
      //-- MODE 1 - Dance Mode!
      //---------------------------------------------------------
      case 1:
        
        randomDance=random(5,21); //5,20
        if((randomDance>14)&&(randomDance<19)){
            randomSteps=1;
            T=1600;
        }
        else{
            randomSteps=random(3,6); //3,5
            T=1000;
        }
        
        Otto.putMouth(random(10,21));

        for (int i=0;i<randomSteps;i++){
            move(randomDance);
            
        }
        break;

      //-- MODE 2 - Obstacle detector mode
      //---------------------------------------------------------
      case 2:

        if(obstacleDetected){
              Otto.putMouth(bigSurprise);
              Otto.sing(S_surprise);
              Otto.jump(5, 500);
              Otto.putMouth(confused);
              Otto.sing(S_cuddly);
            //Otto takes two steps back
            for(int i=0;i<3;i++){ 
            
              Otto.walk(1,1300,-1);
            }

            delay(100);
            obstacleDetector();
            delay(100);
           //If there are no obstacles and no button is pressed, Otto shows a smile
           if(obstacleDetected==true){break;}            
           else{
              Otto.putMouth(smile);
              delay(50);
              obstacleDetector();
           } 
           
           //If there are no obstacles and no button is pressed, Otto shows turns left
           for(int i=0; i<3; i++){
              if(obstacleDetected==true){break;}            
              else{ 
                  Otto.turn(1,1000,1); 
                  obstacleDetector();
              } 
           }
            
            //If there are no obstacles and no button is pressed, Otto is happy
            if(obstacleDetected==true){break;}           
            else{
                Otto.home();
                Otto.putMouth(happyOpen);
                Otto.sing(S_happy_short);
                delay(200);
            }     
        
        }else{

            Otto.walk(1,1000,1); //Otto walk straight
            obstacleDetector();
        }   

        break;

      //-- MODE 3 - Noise detector mode
      //---------------------------------------------------------  
      case 3:
        if (Otto.getNoise()>=650){ //740
          
          delay(50);  //Wait for the possible 'lag' of the button interruptions. 
                      //Sometimes, the noise sensor detect the button before the interruption takes efect 
 
            Otto.putMouth(bigSurprise);
            Otto.sing(S_OhOoh);
            Otto.putMouth(random(10,21));
            randomDance=random(5,21);
            move(randomDance);
            Otto.home();
            delay(500); //Wait for possible noise of the servos while get home
            Otto.putMouth(happyOpen);
        }
        break;
        
      //-- MODE 4 - OttoPAD or any Teleoperation mode (listening SerialPort) 
      //---------------------------------------------------------
      case 4:

        SCmd.readSerial();
        
        //If Otto is moving yet
        if (Otto.getRestState()==false){  
          move(moveId);
        }
      
        break;      

      default:
          MODE=0;
          break;
    }
}  

///////////////////////////////////////////////////////////////////
//-- Functions --------------------------------------------------//
///////////////////////////////////////////////////////////////////

//-- Function to read distance sensor & to actualize obstacleDetected variable
void obstacleDetector(){

   int distance = Otto.getDistance();

        if(distance<15){
          obstacleDetected = true;
        }else{
          obstacleDetected = false;
        }
}

//-- Function to receive Stop command.
void receiveStop(){

    sendAck();
    Otto.home();
    sendFinalAck();

}

//-- Function to receive LED commands
void receiveLED(){  

    //sendAck & stop if necessary
    sendAck();
    Otto.home();

    //Examples of receiveLED Bluetooth commands
    //L 000000001000010100100011000000000
    //L 001111111111111111111111111111111 (todos los LED encendidos)
    unsigned long int matrix;
    char *arg;
    char *endstr;
    arg=SCmd.next();
    //Serial.println (arg);
    if (arg != NULL) {
      matrix=strtoul(arg,&endstr,2);    // Converts a char string to unsigned long integer
      Otto.putMouth(matrix,false);
    }else{
      Otto.putMouth(xMouth);
      delay(2000);
      Otto.clearMouth();
    }

    sendFinalAck();

}

//-- Function to receive buzzer commands
void recieveBuzzer(){
  
    //sendAck & stop if necessary
    sendAck();
    Otto.home(); 

    bool error = false; 
    int frec;
    int duration; 
    char *arg; 
    
    arg = SCmd.next(); 
    if (arg != NULL) { frec=atoi(arg); }    // Converts a char string to an integer   
    else {error=true;}
    
    arg = SCmd.next(); 
    if (arg != NULL) { duration=atoi(arg); } // Converts a char string to an integer  
    else {error=true;}

    if(error==true){

      Otto.putMouth(xMouth);
      delay(2000);
      Otto.clearMouth();

    }else{ 

      Otto._tone(frec, duration, 1);   
    }

    sendFinalAck();

}

//-- Function to receive TRims commands
void receiveTrims(){  

    //sendAck & stop if necessary
    sendAck();
    Otto.home(); 

    int trim_YL,trim_YR,trim_RL,trim_RR;

    //Definition of Servo Bluetooth command
    //C trim_YL trim_YR trim_RL trim_RR
    //Examples of receiveTrims Bluetooth commands
    //C 20 0 -8 3
    bool error = false;
    char *arg;
    arg=SCmd.next();
    if (arg != NULL) { trim_YL=atoi(arg); }    // Converts a char string to an integer   
    else {error=true;}

    arg = SCmd.next(); 
    if (arg != NULL) { trim_YR=atoi(arg); }    // Converts a char string to an integer  
    else {error=true;}

    arg = SCmd.next(); 
    if (arg != NULL) { trim_RL=atoi(arg); }    // Converts a char string to an integer  
    else {error=true;}

    arg = SCmd.next(); 
    if (arg != NULL) { trim_RR=atoi(arg); }    // Converts a char string to an integer  
    else {error=true;}
    
    if(error==true){

      Otto.putMouth(xMouth);
      delay(2000);
      Otto.clearMouth();

    }else{ //Save it on EEPROM
      Otto.setTrims(trim_YL, trim_YR, trim_RL, trim_RR);
      Otto.saveTrimsOnEEPROM(); //Uncomment this only for one upload when you finaly set the trims.
    } 

    sendFinalAck();

}


//-- Function to receive Servo commands
void receiveServo(){  

    sendAck(); 
    moveId = 30;

    //Definition of Servo Bluetooth command
    //G  servo_YL servo_YR servo_RL servo_RR 
    //Example of receiveServo Bluetooth commands
    //G 90 85 96 78 
    bool error = false;
    char *arg;
    int servo_YL,servo_YR,servo_RL,servo_RR;

    arg=SCmd.next();
    if (arg != NULL) { servo_YL=atoi(arg); }    // Converts a char string to an integer   
    else {error=true;}

    arg = SCmd.next(); 
    if (arg != NULL) { servo_YR=atoi(arg); }    // Converts a char string to an integer  
    else {error=true;}

    arg = SCmd.next(); 
    if (arg != NULL) { servo_RL=atoi(arg); }    // Converts a char string to an integer  
    else {error=true;}

    arg = SCmd.next(); 
    if (arg != NULL) { servo_RR=atoi(arg); }    // Converts a char string to an integer  
    else {error=true;}
    
    if(error==true){

      Otto.putMouth(xMouth);
      delay(2000);
      Otto.clearMouth();

    }else{ //Update Servo:

      int servoPos[4]={servo_YL, servo_YR, servo_RL, servo_RR}; 
      Otto._moveServos(200, servoPos);   //Move 200ms
      
    }

    sendFinalAck();

}


//-- Function to receive movement commands
void receiveMovement(){

    sendAck();

    if (Otto.getRestState()==true){
        Otto.setRestState(false);
    }

    //Definition of Movement Bluetooth commands
    //M  MoveID  T   MoveSize  
    char *arg; 
    arg = SCmd.next(); 
    if (arg != NULL) {moveId=atoi(arg);}
    else{
      Otto.putMouth(xMouth);
      delay(2000);
      Otto.clearMouth();
      moveId=0; //stop
    }
    
    arg = SCmd.next(); 
    if (arg != NULL) {T=atoi(arg);}
    else{
      T=1000;
    }

    arg = SCmd.next(); 
    if (arg != NULL) {moveSize=atoi(arg);}
    else{
      moveSize =15;
    }
}


//-- Function to execute the right movement according the movement command received.
void move(int moveId){

  bool manualMode = false;

  switch (moveId) {
    case 0:
      Otto.home();
      break;
    case 1: //M 1 1000 
      Otto.walk(1,T,1);
      break;
    case 2: //M 2 1000 
      Otto.walk(1,T,-1);
      break;
    case 3: //M 3 1000 
      Otto.turn(1,T,1);
      break;
    case 4: //M 4 1000 
      Otto.turn(1,T,-1);
      break;
    case 5: //M 5 1000 30 
      Otto.updown(1,T,moveSize);
      break;
    case 6: //M 6 1000 30
      Otto.moonwalker(1,T,moveSize,1);
      break;
    case 7: //M 7 1000 30
      Otto.moonwalker(1,T,moveSize,-1);
      break;
    case 8: //M 8 1000 30
      Otto.swing(1,T,moveSize);
      break;
    case 9: //M 9 1000 30 
      Otto.crusaito(1,T,moveSize,1);
      break;
    case 10: //M 10 1000 30 
      Otto.crusaito(1,T,moveSize,-1);
      break;
    case 11: //M 11 1000 
      Otto.jump(1,T);
      break;
    case 12: //M 12 1000 30 
      Otto.flapping(1,T,moveSize,1);
      break;
    case 13: //M 13 1000 30
      Otto.flapping(1,T,moveSize,-1);
      break;
    case 14: //M 14 1000 20
      Otto.tiptoeSwing(1,T,moveSize);
      break;
    case 15: //M 15 500 
      Otto.bend(1,T,1);
      break;
    case 16: //M 16 500 
      Otto.bend(1,T,-1);
      break;
    case 17: //M 17 500 
      Otto.shakeLeg(1,T,1);
      break;
    case 18: //M 18 500 
      Otto.shakeLeg(1,T,-1);
      break;
    case 19: //M 19 500 20
      Otto.jitter(1,T,moveSize);
      break;
    case 20: //M 20 500 15
      Otto.ascendingTurn(1,T,moveSize);
      break;
    default:
        manualMode = true;
      break;
  }

  if(!manualMode){
    sendFinalAck();
  }
       
}


//-- Function to receive gesture commands
void receiveGesture(){

    //sendAck & stop if necessary
    sendAck();
    Otto.home(); 

    //Definition of Gesture Bluetooth commands
    //H  GestureID  
    int gesture = 0;
    char *arg; 
    arg = SCmd.next(); 
    if (arg != NULL) {gesture=atoi(arg);}
    else 
    {
      //Otto.putMouth(xMouth);
      delay(2000);
      //Otto.clearMouth();
    }

    switch (gesture) {
      case 1: //H 1 
        Otto.playGesture(OttoHappy);
        break;
      case 2: //H 2 
        Otto.playGesture(OttoSuperHappy);
        break;
      case 3: //H 3 
        Otto.playGesture(OttoSad);
        break;
      case 4: //H 4 
        Otto.playGesture(OttoSleeping);
        break;
      case 5: //H 5  
        Otto.playGesture(OttoFart);
        break;
      case 6: //H 6 
        Otto.playGesture(OttoConfused);
        break;
      case 7: //H 7 
        Otto.playGesture(OttoLove);
        break;
      case 8: //H 8 
        Otto.playGesture(OttoAngry);
        break;
      case 9: //H 9  
        Otto.playGesture(OttoFretful);
        break;
      case 10: //H 10
        Otto.playGesture(OttoMagic);
        break;  
      case 11: //H 11
        Otto.playGesture(OttoWave);
        break;   
      case 12: //H 12
        Otto.playGesture(OttoVictory);
        break; 
      case 13: //H 13
        Otto.playGesture(OttoFail);
        break;         
      default:
        break;
    }

    sendFinalAck();
}

//-- Function to receive sing commands
void receiveSing(){

    //sendAck & stop if necessary
    sendAck();
    Otto.home(); 

    //Definition of Sing Bluetooth commands
    //K  SingID    
    int sing = 0;
    char *arg; 
    arg = SCmd.next(); 
    if (arg != NULL) {sing=atoi(arg);}
    else 
    {
     // Otto.putMouth(xMouth);
      delay(2000);
      //Otto.clearMouth();
    }

    switch (sing) {
      case 1: //K 1 
        Otto.sing(S_connection);
        break;
      case 2: //K 2 
        Otto.sing(S_disconnection);
        break;
      case 3: //K 3 
        Otto.sing(S_surprise);
        break;
      case 4: //K 4 
        Otto.sing(S_OhOoh);
        break;
      case 5: //K 5  
        Otto.sing(S_OhOoh2);
        break;
      case 6: //K 6 
        Otto.sing(S_cuddly);
        break;
      case 7: //K 7 
        Otto.sing(S_sleeping);
        break;
      case 8: //K 8 
        Otto.sing(S_happy);
        break;
      case 9: //K 9  
        Otto.sing(S_superHappy);
        break;
      case 10: //K 10
        Otto.sing(S_happy_short);
        break;  
      case 11: //K 11
        Otto.sing(S_sad);
        break;   
      case 12: //K 12
        Otto.sing(S_confused);
        break; 
      case 13: //K 13
        Otto.sing(S_fart1);
        break;
      case 14: //K 14
        Otto.sing(S_fart2);
        break;
      case 15: //K 15
        Otto.sing(S_fart3);
        break;    
      case 16: //K 16
        Otto.sing(S_mode1);
        break; 
      case 17: //K 17
        Otto.sing(S_mode2);
        break; 
      case 18: //K 18
        Otto.sing(S_mode3);
        break;   
      case 19: //K 19
        Otto.sing(S_buttonPushed);
        break;                      
      default:
        break;
    }

    sendFinalAck();
}


//-- Function to receive Name command
void receiveName(){

    //sendAck & stop if necessary
    sendAck();
    Otto.home(); 

    char newOttoName[11] = "";  //Variable to store data read from Serial.
    int eeAddress = 5;          //Location we want the data to be in EEPROM.
    char *arg; 
    arg = SCmd.next(); 
    
    if (arg != NULL) {

      //Complete newOttoName char string
      int k = 0;
      while((*arg) && (k<11)){ 
          newOttoName[k]=*arg++;
          k++;
      }
      
      EEPROM.put(eeAddress, newOttoName); 
    }
    else 
    {
      //Otto.putMouth(xMouth);
      delay(2000);
      //Otto.clearMouth();
    }

    sendFinalAck();

}


//-- Function to send Otto's name
void requestName(){

    Otto.home(); //stop if necessary

    char actualOttoName[11]= "";  //Variable to store data read from EEPROM.
    int eeAddress = 5;            //EEPROM address to start reading from

    //Get the float data from the EEPROM at position 'eeAddress'
    EEPROM.get(eeAddress, actualOttoName);

    Serial.print(F("&&"));
    Serial.print(F("E "));
    Serial.print(actualOttoName);
    Serial.println(F("%%"));
    Serial.flush();
}


//-- Function to send ultrasonic sensor measure (distance in "cm")
void requestDistance(){

    Otto.home();  //stop if necessary  

    int distance = Otto.getDistance();
    Serial.print(F("&&"));
    Serial.print(F("D "));
    Serial.print(distance);
    Serial.println(F("%%"));
    Serial.flush();
}


//-- Function to send noise sensor measure
void requestNoise(){

    Otto.home();  //stop if necessary

    int microphone= Otto.getNoise(); //analogRead(PIN_NoiseSensor);
    Serial.print(F("&&"));
    Serial.print(F("N "));
    Serial.print(microphone);
    Serial.println(F("%%"));
    Serial.flush();
}


//-- Function to send battery voltage percent
void requestBattery(){

    Otto.home();  //stop if necessary

    //The first read of the batery is often a wrong reading, so we will discard this value. 
    double batteryLevel = Otto.getBatteryLevel();

    Serial.print(F("&&"));
    Serial.print(F("B "));
    Serial.print(batteryLevel);
    Serial.println(F("%%"));
    Serial.flush();
}


//-- Function to send program ID
void requestProgramId(){

    Otto.home();   //stop if necessary

    Serial.print(F("&&"));
    Serial.print(F("I "));
    Serial.print(programID);
    Serial.println(F("%%"));
    Serial.flush();
}


//-- Function to send Ack comand (A)
void sendAck(){

  delay(30);

  Serial.print(F("&&"));
  Serial.print(F("A"));
  Serial.println(F("%%"));
  Serial.flush();
}


//-- Function to send final Ack comand (F)
void sendFinalAck(){

  delay(30);

  Serial.print(F("&&"));
  Serial.print(F("F"));
  Serial.println(F("%%"));
  Serial.flush();
}
//-- Function to receive mode selection.
void requestMode(){

    sendAck();
    Otto.home();
    //Definition of Mode Bluetooth commands
    //J ModeID    
    char *arg; 
    arg = SCmd.next(); 
    if (arg != NULL) 
    {
      modeId=atoi(arg);
      Otto.putMouth(heart);
      }
    else{
      Otto.putMouth(xMouth);
      delay(2000);
      Otto.clearMouth();
      modeId=0; //stop
    }
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

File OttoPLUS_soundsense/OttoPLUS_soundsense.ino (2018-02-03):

//----------------------------------------------------------------
//-- Otto DIY+ soundsense
//-- CC BY SA （ottodiy.com/)
//-----------------------------------------------------------------
#include <Servo.h>
#include <Oscillator.h>
#include <EEPROM.h>

#define N_SERVOS 4
//-- First step: Configure the pins where the servos are attached
/*
         --------------- 
        |     O   O     |
        |---------------|
YR 3==> |               | <== YL 2
         --------------- 
            ||     ||
            ||     ||
RR 5==>   -----   ------  <== RL 4
         |-----   ------|
*/
#define EEPROM_TRIM false 
// Activate to take callibration data from internal memory
#define TRIM_RR 7
#define TRIM_RL 4
#define TRIM_YR  4
#define TRIM_YL -7
//OTTO.setTrims(-7,-4,-4,7);

#define PIN_RR 5
#define PIN_RL 4
#define PIN_YR 3
#define PIN_YL 2

#define INTERVALTIME 10.0 

Oscillator servo[N_SERVOS];

void goingUp(int tempo);
void drunk (int tempo);
void noGravity(int tempo);
void kickLeft(int tempo);
void kickRight(int tempo);
void run(int steps, int T=500);
void walk(int steps, int T=1000);
void backyard(int steps, int T=3000);
void backyardSlow(int steps, int T=5000);
void turnLeft(int steps, int T=3000);
void turnRight(int steps, int T=3000);
void moonWalkLeft(int steps, int T=1000);
void moonWalkRight(int steps, int T=1000);
void crusaito(int steps, int T=1000);
void swing(int steps, int T=1000);
void upDown(int steps, int T=1000);
void flapping(int steps, int T=1000);

int soundDetectedPin = 10; // Use Pin 10 as our Input
int soundDetectedVal = HIGH; // This is where we record our Sound Measurement
boolean bAlarm = false;

unsigned long lastSoundDetectTime; // Record the time that we measured a sound


int soundAlarmTime = 500; // Number of milli seconds to keep the sound alarm high

void setup()
{ 
  pinMode (soundDetectedPin, INPUT) ;
  Serial.begin(19200);
  
  servo[0].attach(PIN_RR);
  servo[1].attach(PIN_RL);
  servo[2].attach(PIN_YR);
  servo[3].attach(PIN_YL);
  
  //EEPROM.write(0,TRIM_RR);
  //EEPROM.write(1,TRIM_RL);
  //EEPROM.write(2,TRIM_YR);
  //EEPROM.write(3,TRIM_YL);
  
  int trim;
  
  if(EEPROM_TRIM){
    for(int x=0;x<4;x++){
      trim=EEPROM.read(x);
      if(trim>128)trim=trim-256;
      Serial.print("TRIM ");
      Serial.print(x);
      Serial.print(" en ");
      Serial.println(trim);
      servo[x].SetTrim(trim);
    }
  }
  else{
    servo[0].SetTrim(TRIM_RR);
    servo[1].SetTrim(TRIM_RL);
    servo[2].SetTrim(TRIM_YR);
    servo[3].SetTrim(TRIM_YL);
  }
  
  for(int i=0;i<4;i++) servo[i].SetPosition(90);
}

// TEMPO: 121 BPM
int t=495;
double pause=0;

void loop()
{
 // if(Serial.available()){
  //  char init = Serial.read();
   // if (init=='X'){
   //   delay(4000); //3000 - 4500
   
dance();


//for(int i=0;i<4;i++) servo[i].SetPosition(90);

      
          for(int i=0;i<4;i++) servo[i].SetPosition(90);
   // }
 // }
}

void dance(){
  soundDetectedVal = digitalRead (soundDetectedPin) ; // read the sound alarm time
  
  if (soundDetectedVal == LOW) // If we hear a sound
  {
  
    lastSoundDetectTime = millis(); // record the time of the sound alarm
    // The following is so you don't scroll on the output screen
    if (!bAlarm){
      Serial.println("LOUD, LOUD");
      bAlarm = true;
  walk(2,t*2);
    }
  }
    else
  {
    if( (millis()-lastSoundDetectTime) > soundAlarmTime  &&  bAlarm){
      Serial.println("quiet");
      bAlarm = false;
    }
}
}


////////////////////////////////////////////////////////////////////////////////////////
//////////////////////////////////FUNCIONES DE CONTROL//////////////////////////////////
////////////////////////////////////////////////////////////////////////////////////////

void oscillate(int A[N_SERVOS], int O[N_SERVOS], int T, double phase_diff[N_SERVOS]){
  for (int i=0; i<4; i++) {
    servo[i].SetO(O[i]);
    servo[i].SetA(A[i]);
    servo[i].SetT(T);
    servo[i].SetPh(phase_diff[i]);
  }
  double ref=millis();
   for (double x=ref; x<T+ref; x=millis()){
     for (int i=0; i<4; i++){
        servo[i].refresh();
     }
  }
}

unsigned long final_time;
unsigned long interval_time;
int oneTime;
int iteration;
float increment[N_SERVOS]; 
int oldPosition[]={90,90,90,90};

void moveNServos(int time, int  newPosition[]){
  for(int i=0;i<N_SERVOS;i++)	increment[i] = ((newPosition[i])-oldPosition[i])/(time/INTERVALTIME);
  
  final_time =  millis() + time; 
  
  iteration = 1; 
  while(millis() < final_time){ //Javi del futuro cambia esto  
      interval_time = millis()+INTERVALTIME;  
      
      oneTime=0;      
      while(millis()<interval_time){	  
          if(oneTime<1){ 
              for(int i=0;i<N_SERVOS;i++){
                  servo[i].SetPosition(oldPosition[i] + (iteration * increment[i]));
              }			
              iteration++;
              oneTime++;
          }
      }     
  }   

  for(int i=0;i<N_SERVOS;i++){	
    oldPosition[i] = newPosition[i];
  }   
}


//////////////////////////////////////////////////////////////////////////////
////////////////////////////////PASOS DE BAILE////////////////////////////////
//////////////////////////////////////////////////////////////////////////////

void goingUp(int tempo){
  
      pause=millis();
      for(int i=0;i<4;i++) servo[i].SetPosition(90);
      delay(tempo);
      servo[0].SetPosition(80);
      servo[1].SetPosition(100);
      delay(tempo);
      servo[0].SetPosition(70);
      servo[1].SetPosition(110);
      delay(tempo);
      servo[0].SetPosition(60);
      servo[1].SetPosition(120);
      delay(tempo);
      servo[0].SetPosition(50);
      servo[1].SetPosition(130);
      delay(tempo);
      servo[0].SetPosition(40);
      servo[1].SetPosition(140);
      delay(tempo);
      servo[0].SetPosition(30);
      servo[1].SetPosition(150);
      delay(tempo);
      servo[0].SetPosition(20);
      servo[1].SetPosition(160);
      delay(tempo);
      
      while(millis()<pause+8*t);

}

void primera_parte(){
  
  int move1[4] = {60,120,90,90};
  int move2[4] = {90,90,90,90};
  int move3[4] = {40,140,90,90};
  
  for(int x=0; x<3; x++){
    for(int i=0; i<3; i++){
      lateral_fuerte(1,t/2);
      lateral_fuerte(0,t/4);
      lateral_fuerte(1,t/4);
      delay(t);
    }
  
    pause=millis();
    for(int i=0;i<4;i++) servo[i].SetPosition(90);
    moveNServos(t*0.4,move1);
    moveNServos(t*0.4,move2);
    while(millis()<(pause+t*2));
  }
  
  for(int i=0; i<2; i++){
    lateral_fuerte(1,t/2);
    lateral_fuerte(0,t/4);
    lateral_fuerte(1,t/4);
    delay(t);
  }
    
  pause=millis();
  for(int i=0;i<4;i++) servo[i].SetPosition(90);
  crusaito(1,t*1.4);
  moveNServos(t*1,move3);
  for(int i=0;i<4;i++) servo[i].SetPosition(90);
  while(millis()<(pause+t*4));
}
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

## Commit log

2017-05-17 3d .stl, and APP screenshots
    [Body_MATRIX_4.stl, Head_MATRIX_5.stl, OTTO_body_v5.stl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]
2017-05-17 Arduino codes
2017-05-17 PCB (optional)
    [otto.brd, otto.sch]
2017-05-17 libraries for arduino
2017-08-22 Hall of fame Otto builders list
    overview of the remarkable contributions to Otto DIY
2017-08-22 Hall of fame Otto builders list
2017-09-18 Jason Snow PCB design
2018-02-03 touch
    touch in pin 12 with random dance moves after every touch

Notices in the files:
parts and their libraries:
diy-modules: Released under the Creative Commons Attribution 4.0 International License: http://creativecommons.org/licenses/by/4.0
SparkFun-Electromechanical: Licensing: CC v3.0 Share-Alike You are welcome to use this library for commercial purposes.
